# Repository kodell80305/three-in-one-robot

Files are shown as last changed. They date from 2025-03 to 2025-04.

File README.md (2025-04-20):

# three-in-one-robot

I've completed two of the three robots I had planned for this project.  The 40 cm SCARA version:



and what is pretty much a version of the Dune Weaver Robot:



I need to work on the software for the SCARA robot ... I'm planning on doing a version of the Dune Weaver software that will support this.  I also need to get the software for the DW radial arm version done.   Both of the robots need a little more work on the limit switches ... in the 40 cm SCARA case, I just need to add the optical detector for the rotary & elbow motor.   In the radial arm case, the rotary is pretty easy, but the hall effect limit switch I need to use for the radial arm is very tight.

The goal in this project is to develop a fully parameterized rotational platform that can be used for a few projects I'm doing.

 1. The first one is a 40 cm SCARA robot.   My original sand table was done using a SCARA robot I found from the "Always Tinkering" blog by Matt G.   This was based on work by Rob Dobson.  (I'll do the links later).   I actually built two coffee table size versions (one for me and one for my son).    I was never completely happy with a few aspects - mostly due to my lack of experience in 3d printing, 3d modeling.   It was difficult (for me!) to get the arm lengths correct and to get the belt tension correct.   I ported the software to the dlc32 board and added support for addressable leds and a serial smart screen.    I wanted a smaller SCARA robot to use to get the Dune Weaver software running and abandon my previous efforts (because Tuan's software and architecture is much better than what I have)

 2. The second will be a Dune Weaver - style radial arm convert my table to.  The design here won't be too origina it's very similar to the Dune Weaver Pro - I'll need to split the arm in two, so it will be supported by 5 mm carbon fiber rods.   I've already designed and build one of these, so this will be pretty quick.   I'll have support for a rotational optical switch and a hall effect central switch.  I have not tried the sensorless homing used by the Dune Weaver folks, ut that is an option.

 3. The third drops the central motor entirely and just uses the rotational portion ... it would be for a image-to-string project to implement an algorithm my son wrote.

(I actually want to do a fourth, which would be a full size SCARA robot and I have a design in mind for a Ombonad-size SCARA robot with a differential that I really want to do ...)

So, what's the point of all this?

In programming terms, what I want to do is design a "base class" that you could use to create derived classes for a particular purpose.   All of these will use a lazy susan (of various sizes), a support for the lazy susan, support for optical sensing, support for different size of stepping motors (but all NEMA 17) and implementations of 15, 24, 150, 180, 240 tooth gears, GT2 gears, etc.   The idea is that you can chose whatever makes sense for your application ... you just need to design whatever needs to attach to the outer lazy susan.   I'll document the 40 cm SCARA version and hopefully this will make sense.

The 40 cm SCARA turned out to be an interesting choice for a first test ... due to the constraints of where the elbow needed to be I ended up with a six inch lazy susan, but a 240 tooth/240 mm pitch diameter outer gear.   The elbow sits between the support for the lazy susan (which is the inner ring) and the rotational motor.

In real, practcial terms what I've found is that using parameters on this project has been the single biggest improvement to my Fusion 360 skills and organization.   It's really just a list of all the variables that go into your design and their values.   Using parameters means:

1. I've thought through what the important constraints/numbers are & am consistent across the design.
2. I tend to do many more, simpler sketches - before I was trying to cram everything into a single sketch
3. I don't use projection geometry
4. I'm consistent across the sketches
5. My error rate is a fraction of what is was before.

This is a work in progress (as of March 2025), so I'll be updating this fairly   I'm mostly doing this at least partially as an exercise to improve my 3d modeling skills. 

Status:

The Ombonad robot is complete - but I just realized that once again I was making life way too hard so I have one change I want to make.  The plan is to get this working, go back and tweak the base platform to fix some weaknesses and then start on what is essentially a copy of the Dune Weaver Pro to fit my table.

Critical constraints/vertical

Rotary gear needs to mesh with the main gear.

Height of rotary = Top of main gear - clearance (it should be at least 1 mm below top)
                 = base thickness + Motor length

*** So MainTop = BaseHeight + NemaML + Clearance 

Second would be that the Lazy Susan support + Lazy SusanHeight + MainGearHeight = MainTop
So MainTop = LZSupportHeight + LZHeight + MainGearHeight,

***Computed: LZSupportHeight = BaseHeight + NemaML + Clearance - LZHeight - MainGearHeight

Lazy Susan support starts at BaseHeight & is (BaseHeight + NemaML + Clearance - LZHeight - MainGearHeight)

where BaseHeight just for additional support, I'm using 3 mm here.
NEMA motor length depends on motors chosen, I'm using some pancake steppers for this.
Clearance is 1 mm
LZ Height is the purchased Lazy Susan - 8.5 mm
MainGear Height is chosen to be 8 mm (it won't effect the overall robot height - actually the thicker the main gear the lower the robot in this particular case)

1. Change bearing size to 21x15
2. Get rid of m3 heat inserts - use generic m3hole size of 2.7 mm for "self tapping" holes

3. Arm guide = Top is at MainTop - MainThickness, bottom at MainTop - MainThickness - ArmGuideHeight

Arm redesign

Shaft is inner diameter of bearing
Need a circle size of gt2 40 tooth pully

Assume bottom of rotary is zero:

ML - RotaryHeight = MainBottomHeight

Constraint 1: Rotary Motor should mesh with main gear ... bottom of rotary should line up with bottom of main gear (main gear is taller, so provides clearance)

MainBottom = ML - RotaryHeight
MainBottom = SupportHeight + LazySusanHeight

ML - depends on what motor is picked
LazySusanHeight - depends on manufacturer of lazy susan

So SupportHeight = ML - RotaryHeight - LazySusanHeight

Radial motor:

GTHeight should include shim for clearance, so call in 10 mm
End of motor - GT2 Height = MainTopEffective  <- same level as gear driving outer arm ... we don't need clearance, but we do on outer arm

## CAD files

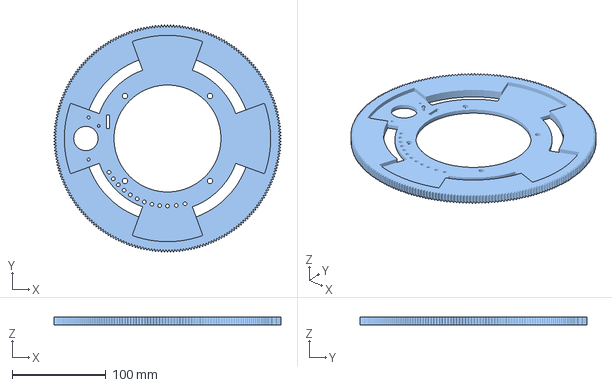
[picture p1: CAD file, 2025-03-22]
40cmScaraSixInchLZPancake/3dModels/SCARA40cmMainGear.3mf
242.0 x 242.0 x 8.00 mm

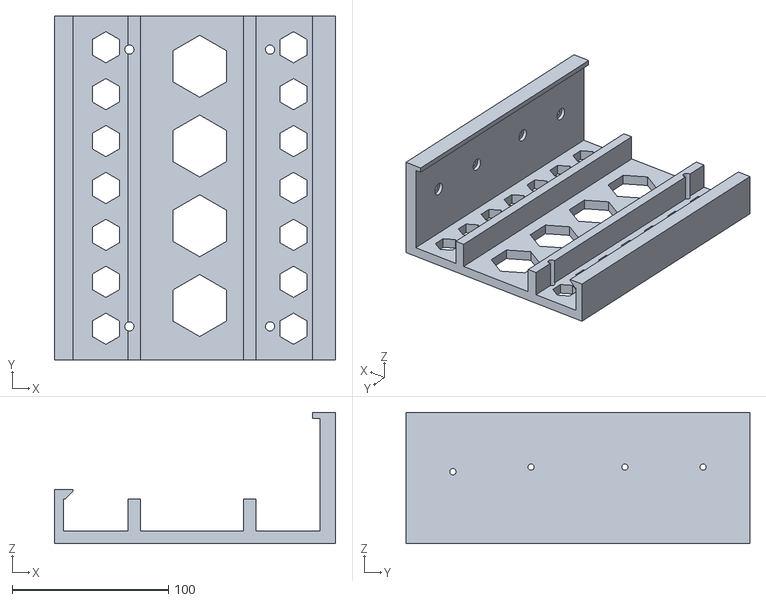
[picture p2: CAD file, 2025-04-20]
RadialArm/Wii Main Bracket.stl
180.0 x 220.0 x 84.0

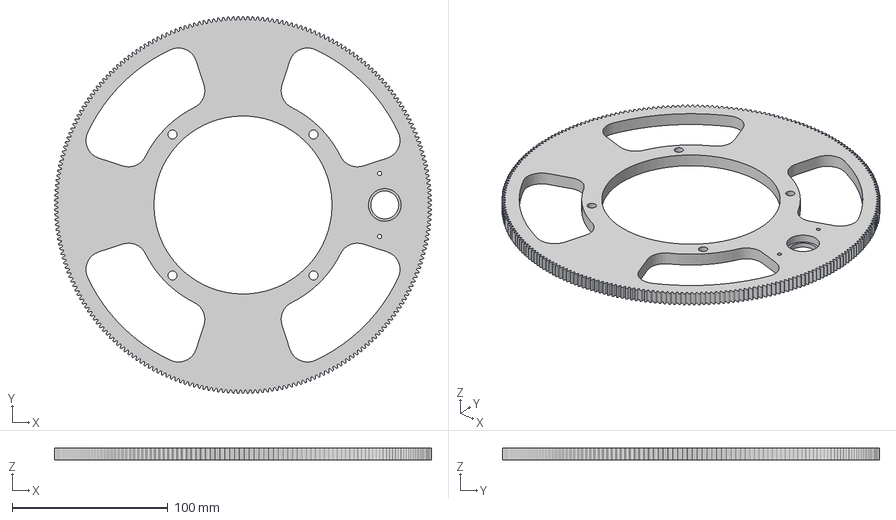
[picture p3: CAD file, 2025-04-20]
40cmScara/240ToothScara.3mf
242.0 x 242.0 x 8.00 mm

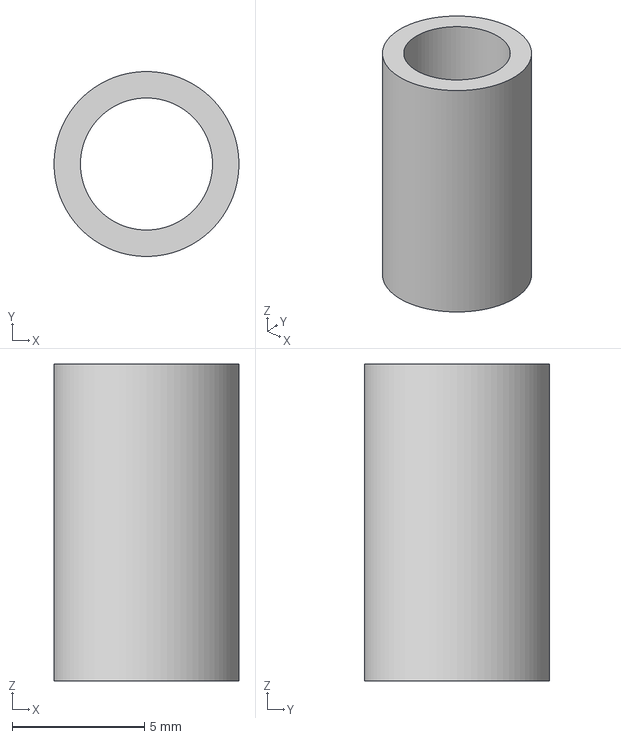
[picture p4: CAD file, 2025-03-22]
40cmScaraSixInchLZPancake/3dModels/IdleSleeve.3mf
7.00 x 7.00 x 12.0 mm

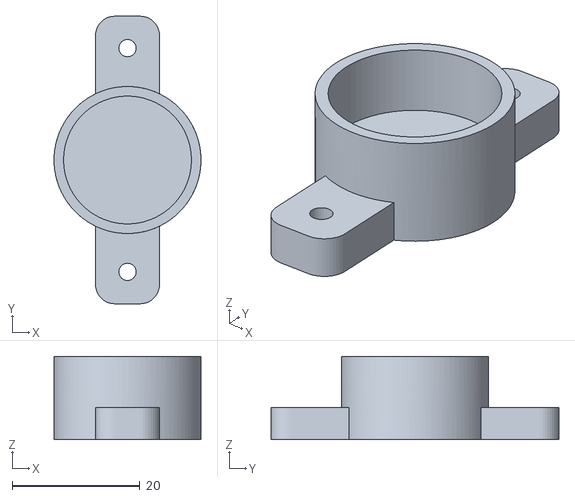
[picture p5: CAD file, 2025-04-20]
RadialArm/magnetHolder.stl
23.0 x 45.0 x 13.0

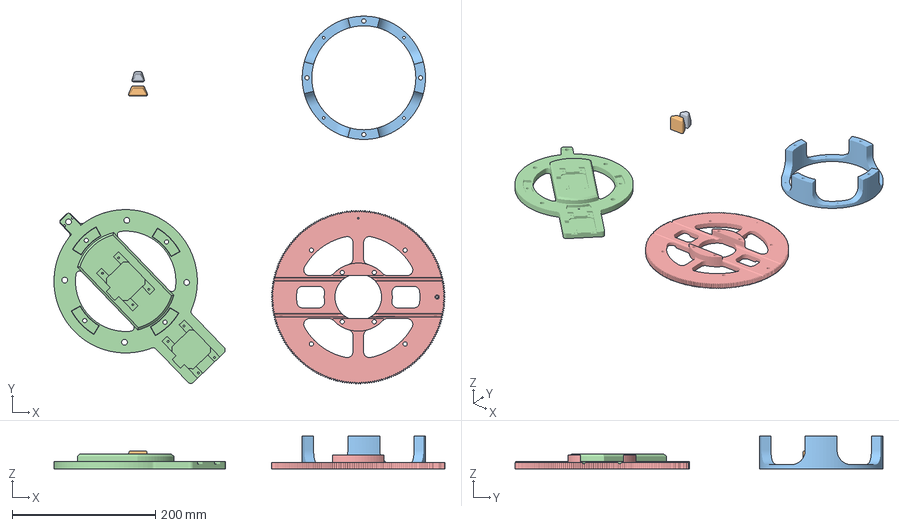
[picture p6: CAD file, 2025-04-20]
RadialArmEightInch.3mf
545.5 x 512.9 x 45.5 mm
SunYearGusset.stl x 2
LazySusanSupport.stl
SupportBase.stl
240ToothRadial.stl

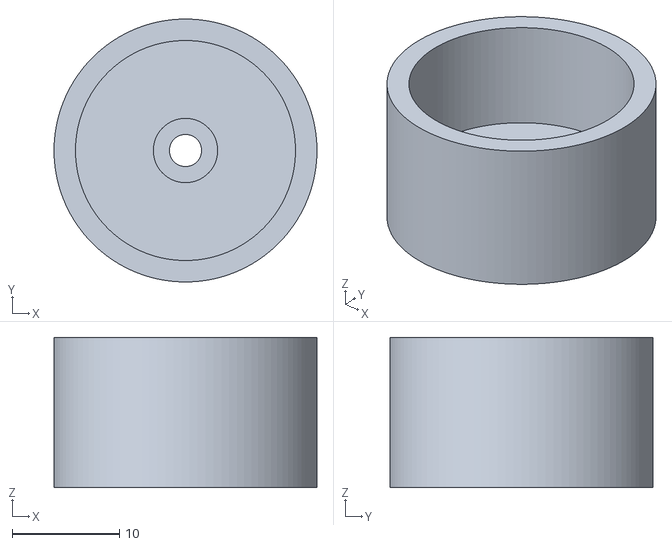
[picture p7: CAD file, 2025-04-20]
40cmScara/MagnetHolder.stl
24.5 x 24.5 x 14.0

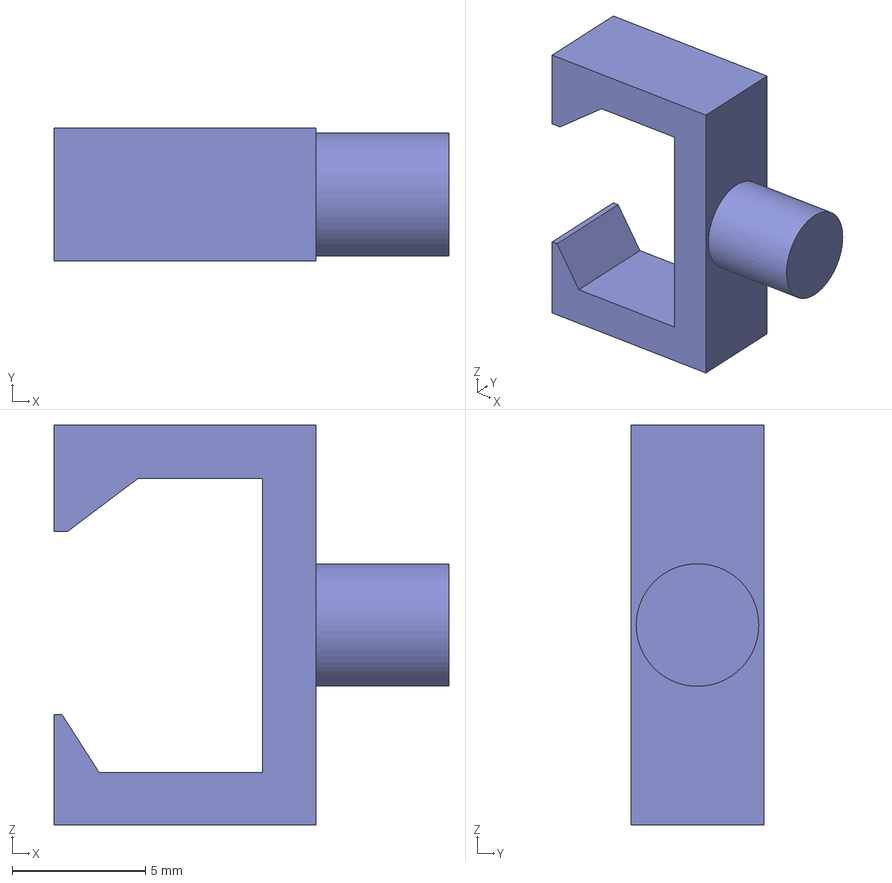
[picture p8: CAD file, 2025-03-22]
40cmScaraSixInchLZPancake/3dModels/led holder.3mf
14.8 x 5.00 x 15.0 mm

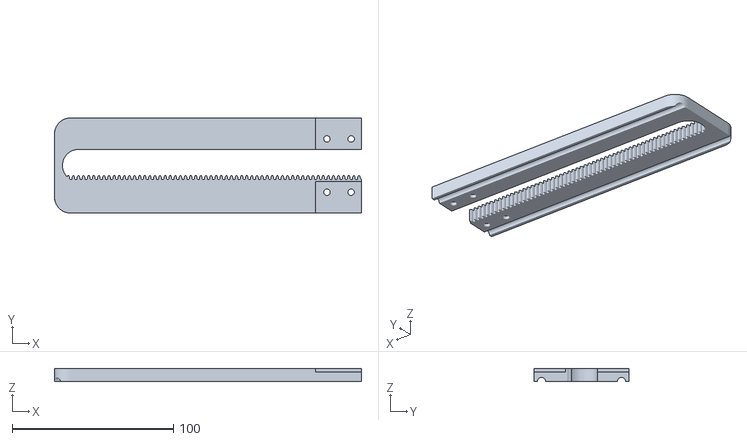
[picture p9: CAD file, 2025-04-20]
RadialArm/rightArm.stl
190.2 x 59.0 x 8.00

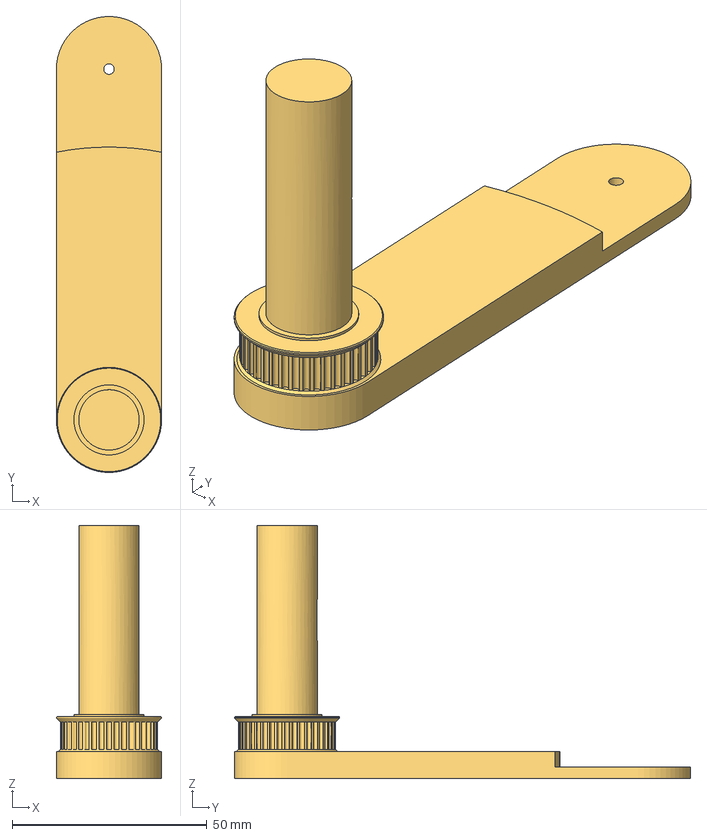
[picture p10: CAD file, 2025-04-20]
40cmScara/OuterArm.3mf
27.0 x 117.0 x 65.0 mm

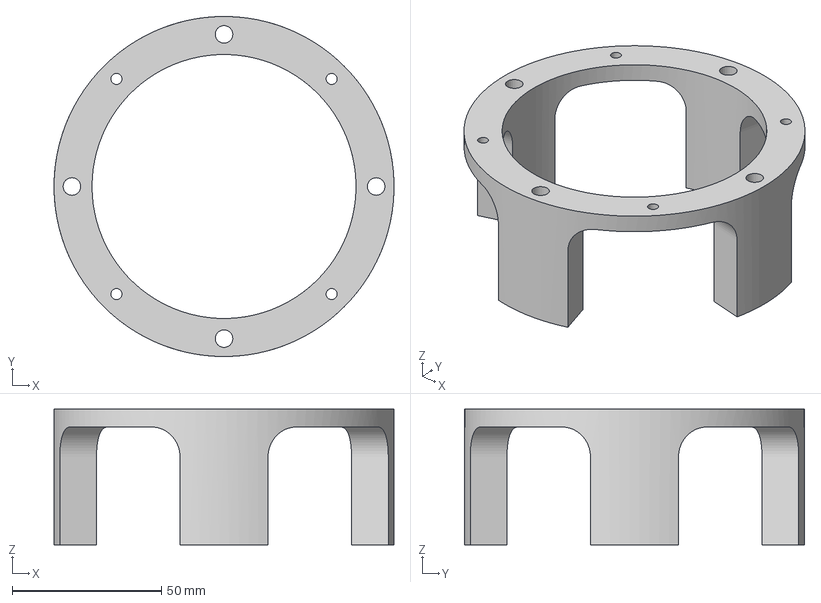
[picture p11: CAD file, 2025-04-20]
40cmScara/LazySusanSupport.3mf
114.0 x 114.0 x 45.5 mm

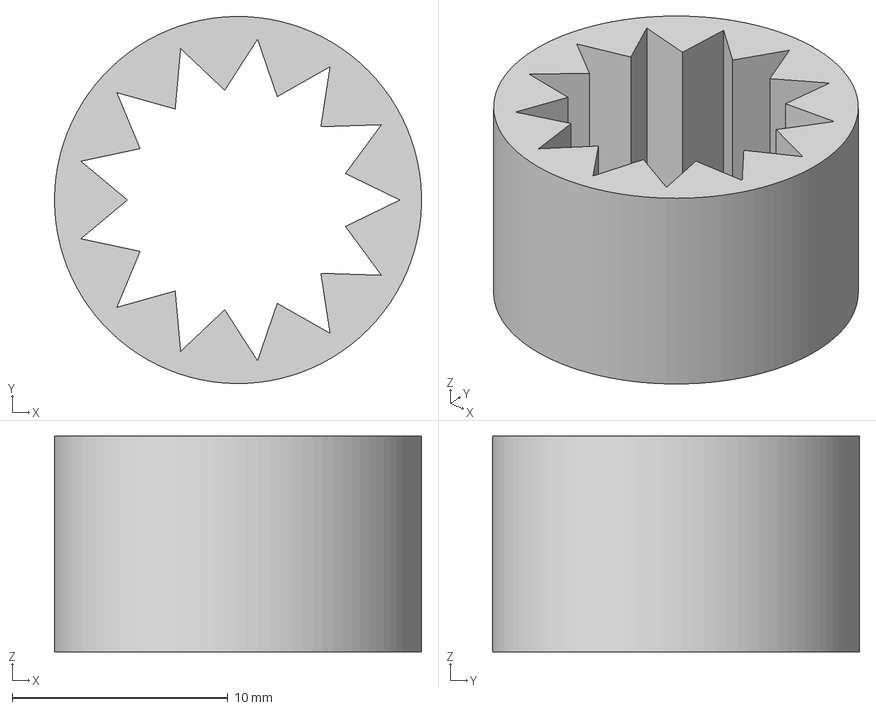
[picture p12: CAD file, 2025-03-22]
40cmScaraSixInchLZPancake/3dModels/OutArmSleeve.3mf
17.0 x 17.0 x 10.0 mm

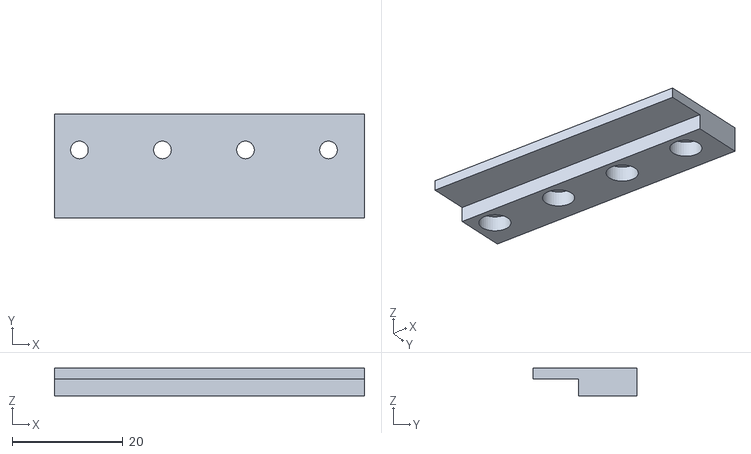
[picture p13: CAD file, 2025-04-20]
RadialArm/frontJoiner.stl
56.0 x 18.8 x 5.00

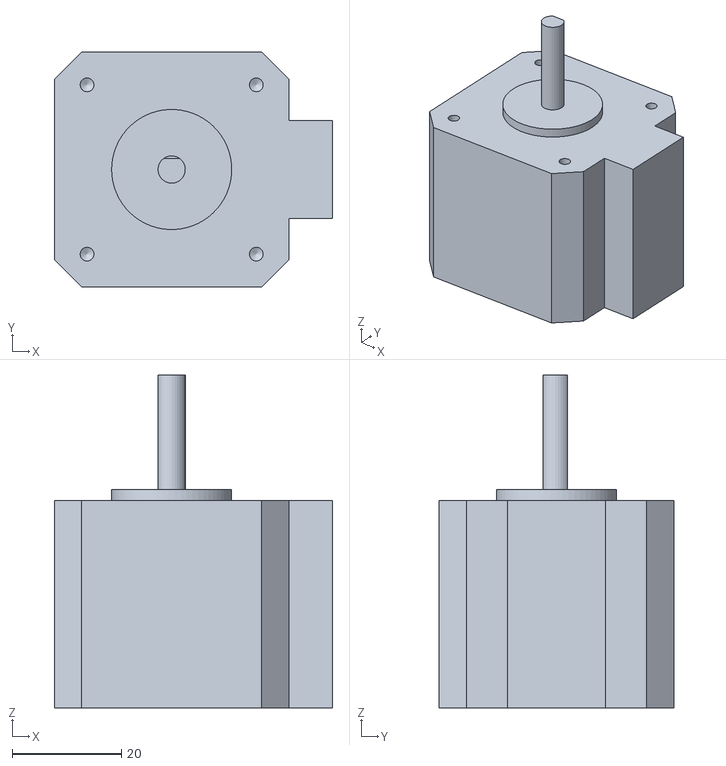
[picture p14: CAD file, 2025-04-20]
40cmScara/NemaRad.stl
51.0 x 43.0 x 61.0

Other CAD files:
40cmScaraSixInchLZPancake/3dModels/GT2 Center.3mf
40cmScara/arm guide.3mf
40cmScaraSixInchLZPancake/3dModels/Lazy Susan Support.3mf
RadialArm/Body1.stl
40cmScara/EndCap.stl
40cmScara/NemaBracket.3mf
40cmScara/NemaRot.3mf
40cmScara/SupportBase.3mf
40cmScaraSixInchLZPancake/3dModels/24ToothRotary.3mf
40cmScaraSixInchLZPancake/3dModels/GT2 Pulley.3mf
40cmScaraSixInchLZPancake/3dModels/GT2 elbow pulley.3mf
40cmScaraSixInchLZPancake/3dModels/GT2IdlePully.3mf
40cmScaraSixInchLZPancake/3dModels/OuterArm.3mf
40cmScaraSixInchLZPancake/3dModels/OuterArmEndcap.3mf
40cmScaraSixInchLZPancake/3dModels/OuterArmGuide.3mf
40cmScaraSixInchLZPancake/3dModels/SupportRingOne.3mf
RadialArm/15toothRad.stl
RadialArm/240ToothRadial.stl
RadialArm/24toothRot.stl
RadialArm/Body4.stl
RadialArm/LazySusanSupport.stl
RadialArm/NemaBracket.stl
RadialArm/SupportBase.stl
RadialArm/WiiBracketVesa.stl
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

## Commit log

2025-03-22 First creation from base class
    Overall, it took around 5-6 hours to create this from the base class - some of this was due to the constraints of trying to fit the elbow arm in the right spot .... a
    [24ToothRotary.3mf, GT2 Center.3mf, GT2 Pulley.3mf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]
2025-04-20 Update with current radial arm & ombonad scara
    These are two of the three robots I have planned. (I'll defer the string art until I have got the software for both of these working.
    [15toothRad.stl, 240ToothRadial.stl, 240ToothScara.3mf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]
